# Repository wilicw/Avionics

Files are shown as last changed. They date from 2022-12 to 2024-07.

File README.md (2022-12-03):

# Avionics System

## Get Started

### [Install PlatformIO CLI](https://docs.platformio.org/en/latest/)

### Build Source Code

```
make
```

### Upload

```
make upload
```

## System Architecture

## [LICENSE](https://github.com/NCKU-ISP/Avionics/blob/main/LICENSE)

## Contact Us

To report any bugs or commit any new features, please create a new pull request and describe the issues in detail. If you are interested in our project and want to support us, please contact us with the following email: e94066157@gs.ncku.edu.tw, thanks!

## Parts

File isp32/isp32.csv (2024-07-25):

Source: | /Users/wilicw/Projects/Avionics-PCB/isp32/isp32.kicad_sch
Date: | Tuesday, June 04, 2024 at 09:10:36 PM
Tool: | Eeschema 7.0.11
Generator: | /Applications/KiCad/KiCad.app/Contents/SharedSupport/plugins/bom_csv_grouped_by_value.py
Component Count: | 85
Collated Components:
Item | Qty | Reference(s) | Value | LibPart | Footprint | Datasheet | DNP | MANUFACTURER | MAXIMUM_PACKAGE_HEIGHT | PARTREV | STANDARD | Sim.Device | Sim.Pins
1 | 6 | C3, C9, C11, C13, C16, C23 | 100n | Device:C_Small | Capacitor_SMD:C_0603_1608Metric | ~
2 | 1 | C5 | 100n | Device:C_Small | Capacitor_SMD:C_0805_2012Metric | ~
3 | 2 | C6, C10 | 22u | Device:C_Small | Capacitor_SMD:C_0603_1608Metric | ~
4 | 1 | C12 | 220u | Device:C_Small | Capacitor_Tantalum_SMD:CP_EIA-3528-12_Kemet-T | ~
5 | 2 | C14, C22 | 1u | Device:C_Small | Capacitor_SMD:C_0603_1608Metric | ~
6 | 1 | C15 | 10u | Device:C_Small | Capacitor_SMD:C_0805_2012Metric | ~
7 | 1 | D1 | Zener | Device:D_Zener_Small | Diode_SMD:D_SOD-123 | ~
8 | 1 | D2 | F0_LED | Device:LED_Small | LED_SMD:LED_0603_1608Metric | ~
9 | 1 | D3 | ESP_LED | Device:LED_Small | LED_SMD:LED_0603_1608Metric | ~
10 | 1 | D4 | F1_LED | Device:LED_Small | LED_SMD:LED_0603_1608Metric | ~
11 | 1 | D5 | POWER | Device:LED_Small | LED_SMD:LED_0603_1608Metric | ~
12 | 1 | D6 | TVS | Device:D_TVS_Filled | Diode_SMD:D_SMB | ~
13 | 1 | D7 | WS2812B | LED:WS2812B | LED_SMD:LED_WS2812B_PLCC4_5.0x5.0mm_P3.2mm | https://cdn-shop.adafruit.com/datasheets/WS2812B.pdf
14 | 1 | D8 | D_Shockley | Device:D_Shockley | Diode_SMD:D_SOD-123 | ~
15 | 1 | D9 | D_Small | Device:D_Small | Diode_SMD:D_SOD-123 | ~ |  |  |  |  |  | D | 1=K 2=A
16 | 4 | H1, H2, H3, H4 | MountingHole_Pad | Mechanical:MountingHole_Pad | MountingHole:MountingHole_3.2mm_M3_ISO7380_Pad | ~
17 | 1 | J1 | BAT1 | Connector_Generic:Conn_01x02 | Connector_JST:JST_XH_S2B-XH-A-1_1x02_P2.50mm_Horizontal | ~
18 | 1 | J2 | ExtBoard | Connector_Generic_MountingPin:Conn_01x05_MountingPin | Connector_Molex:Molex_PicoBlade_53261-0571_1x05-1MP_P1.25mm_Horizontal | ~
19 | 1 | J3 | USB_C_Receptacle_USB2.0 | Connector:USB_C_Receptacle_USB2.0 | Connector_USB:USB_C_Receptacle_Palconn_UTC16-G | https://www.usb.org/sites/default/files/documents/usb_type-c.zip
20 | 1 | J4 | ADC | Connector_Generic:Conn_01x05 | Connector_PinHeader_1.27mm:PinHeader_1x05_P1.27mm_Vertical | ~
21 | 1 | J5 | GPS_ANT | Connector:Conn_Coaxial | Connector_Coaxial:U.FL_Hirose_U.FL-R-SMT-1_Vertical | ~
22 | 1 | J6 | F0 | Connector:Screw_Terminal_01x02 | TerminalBlock_Phoenix:TerminalBlock_Phoenix_MPT-0,5-2-2.54_1x02_P2.54mm_Horizontal | ~
23 | 1 | J7 | F1 | Connector:Screw_Terminal_01x02 | TerminalBlock_Phoenix:TerminalBlock_Phoenix_MPT-0,5-2-2.54_1x02_P2.54mm_Horizontal | ~
24 | 1 | J9 | ANT | Connector_Generic:Conn_01x01 | Connector_PinHeader_2.00mm:PinHeader_1x01_P2.00mm_Vertical | ~
25 | 1 | J10 | LoRa_ANT | Connector:Conn_Coaxial | Connector_Coaxial:U.FL_Hirose_U.FL-R-SMT-1_Vertical | ~
26 | 1 | J11 | Power Modules | Connector_Generic:Conn_01x04 | Connector_PinSocket_2.54mm:PinSocket_1x04_P2.54mm_Vertical | ~
27 | 1 | J12 | Micro_SD_Card | Connector:Micro_SD_Card | Connector_Card:microSD_HC_Wuerth_693072010801 | http://katalog.we-online.de/em/datasheet/693072010801.pdf
28 | 1 | J13 | VIN_SELECT | Connector_Generic:Conn_01x03 | Connector_PinHeader_2.54mm:PinHeader_1x03_P2.54mm_Vertical | ~
29 | 1 | J14 | BUZZ | Connector_Generic_MountingPin:Conn_01x02_MountingPin | Connector_Molex:Molex_PicoBlade_53261-0271_1x02-1MP_P1.25mm_Horizontal | ~
30 | 1 | L2 | 22u | Device:L_Small | Inductor_SMD:L_0805_2012Metric | ~
31 | 1 | LS1 | 5020 | KSSG33J12-3:KSSG33J12-3 | Buzzer:XDCR_KSSG33J12-3 |  |  | Kingstate | 2.2 mm | 1.4 | Manufacturer recommendations
32 | 4 | M1, M2, M3, M4 | Motor_Servo | Motor:Motor_Servo | Connector_PinHeader_2.54mm:PinHeader_1x03_P2.54mm_Vertical | http://forums.parallax.com/uploads/attachments/46831/74481.png
33 | 2 | Q1, Q4 | BSS138 | Transistor_FET:BSS138 | Package_TO_SOT_SMD:SOT-23 | https://www.onsemi.com/pub/Collateral/BSS138-D.PDF
34 | 1 | Q2 | S8050 | Device:Q_NPN_BCE | Package_TO_SOT_SMD:SOT-23 | ~
35 | 3 | Q3, Q5, Q6 | IRLML6402 | Transistor_FET:IRLML6402 | Package_TO_SOT_SMD:SOT-23 | https://www.infineon.com/dgdl/irlml6402pbf.pdf?fileId=5546d462533600a401535668d5c2263c
36 | 6 | R1, R2, R14, R15, R22, R25 | 10k | Device:R_Small | Resistor_SMD:R_0603_1608Metric | ~
37 | 1 | R3 | 100 | Device:R_Small | Resistor_SMD:R_0603_1608Metric | ~
38 | 2 | R4, R6 | 4k7 | Device:R_Small | Resistor_SMD:R_0603_1608Metric | ~
39 | 2 | R5, R7 | 5k1 | Device:R_Small | Resistor_SMD:R_0603_1608Metric | ~
40 | 1 | R12 | 22 | Device:R_Small | Resistor_SMD:R_0603_1608Metric | ~
41 | 4 | R16, R20, R23, R24 | 100K | Device:R_Small | Resistor_SMD:R_0603_1608Metric | ~
42 | 2 | R18, R19 | 1k | Device:R_Small | Resistor_SMD:R_0603_1608Metric | ~
43 | 1 | R26 | 100k | Device:R_Small | Resistor_SMD:R_0603_1608Metric | ~
44 | 1 | SW1 | RST | Switch:SW_Push | Button_Switch_SMD:SW_SPST_FSMSM | ~
45 | 1 | TP1 | 3V3 | Connector:TestPoint | TestPoint:TestPoint_Pad_D1.0mm | ~
46 | 1 | TP2 | TP-3V3 | Connector:TestPoint | TestPoint:TestPoint_Pad_D1.0mm | ~
47 | 1 | TP3 | SWDIO | Connector:TestPoint | TestPoint:TestPoint_Pad_D1.0mm | ~
48 | 1 | TP4 | SWCLK | Connector:TestPoint | TestPoint:TestPoint_Pad_D1.0mm | ~
49 | 1 | TP5 | GND | Connector:TestPoint | TestPoint:TestPoint_Pad_D1.0mm | ~
50 | 1 | U1 | AZ1117-3.3 | Regulator_Linear:AZ1117-3.3 | Package_TO_SOT_SMD:SOT-223-3_TabPin2 | https://www.diodes.com/assets/Datasheets/AZ1117.pdf
51 | 1 | U2 | BA05C | Regulator_Linear:AP2204R-5.0 | Package_TO_SOT_SMD:TO-252-2 | https://www.diodes.com/assets/Datasheets/AP2204.pdf
52 | 1 | U3 | STM32G030F6 | STM32G030F6:STM32G030F6 | Package_SO:TSSOP-20_4.4x6.5mm_P0.65mm
53 | 1 | U4 | LSM6DSM | Sensor_Motion:LSM6DSM | Package_LGA:LGA-14_3x2.5mm_P0.5mm_LayoutBorder3x4y | https://www.st.com/resource/en/datasheet/lsm6dsm.pdf
54 | 1 | U6 | 24LC32 | Memory_EEPROM:24LC32 | Package_SO:SOIC-8_3.9x4.9mm_P1.27mm | http://ww1.microchip.com/downloads/en/DeviceDoc/21072G.pdf
55 | 1 | U7 | NEO-XM | RF_GPS:NEO-M8M | RF_GPS:ublox_NEO | https://www.u-blox.com/sites/default/files/NEO-M8-FW3_DataSheet_%28UBX-15031086%29.pdf
56 | 1 | U8 | ESP32-S3-WROOM-1U | ESP32-S3-WROOM-1U:ESP32-S3-WROOM-1U | ESP32-S3-WROOM-1U:XCVR_ESP32-S3-WROOM-1U |  |  | Espressif | 3.35mm | v0.6 | Manufacturer Recommendations
57 | 1 | U9 | RFM98W-315S2 | RF_Module:RFM98W-315S2 | RF_Module:HOPERF_RFM9XW_SMD | https://www.hoperf.com/data/upload/portal/20181127/5bfcdb5e17543.pdf
58 | 1 | U10 | BMP280 | Sensor_Pressure:BMP280 | Package_LGA:Bosch_LGA-8_2x2.5mm_P0.65mm_ClockwisePinNumbering | https://ae-bst.resource.bosch.com/media/_tech/media/datasheets/BST-BMP280-DS001.pdf

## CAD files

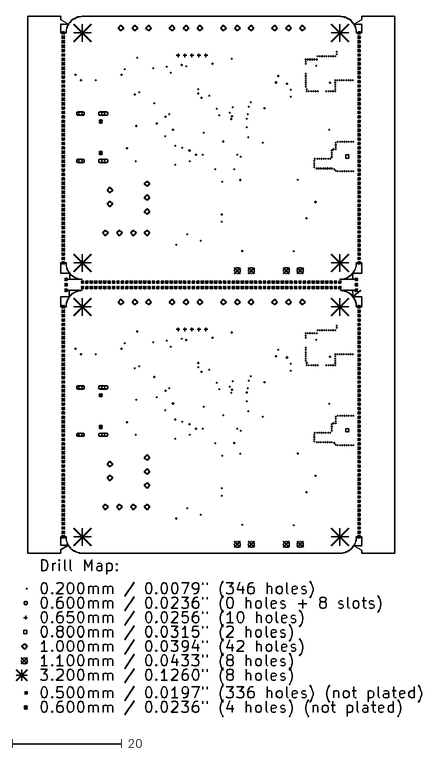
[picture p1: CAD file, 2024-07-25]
isp32/gerber/panel-drl_map.dxf
73.9 x 127.8

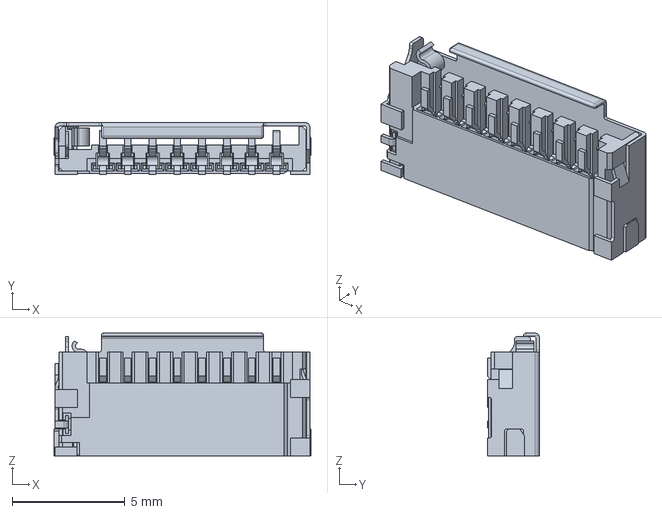
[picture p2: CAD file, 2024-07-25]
isp32/475710001.stp
11.4 x 2.30 x 5.45 mm

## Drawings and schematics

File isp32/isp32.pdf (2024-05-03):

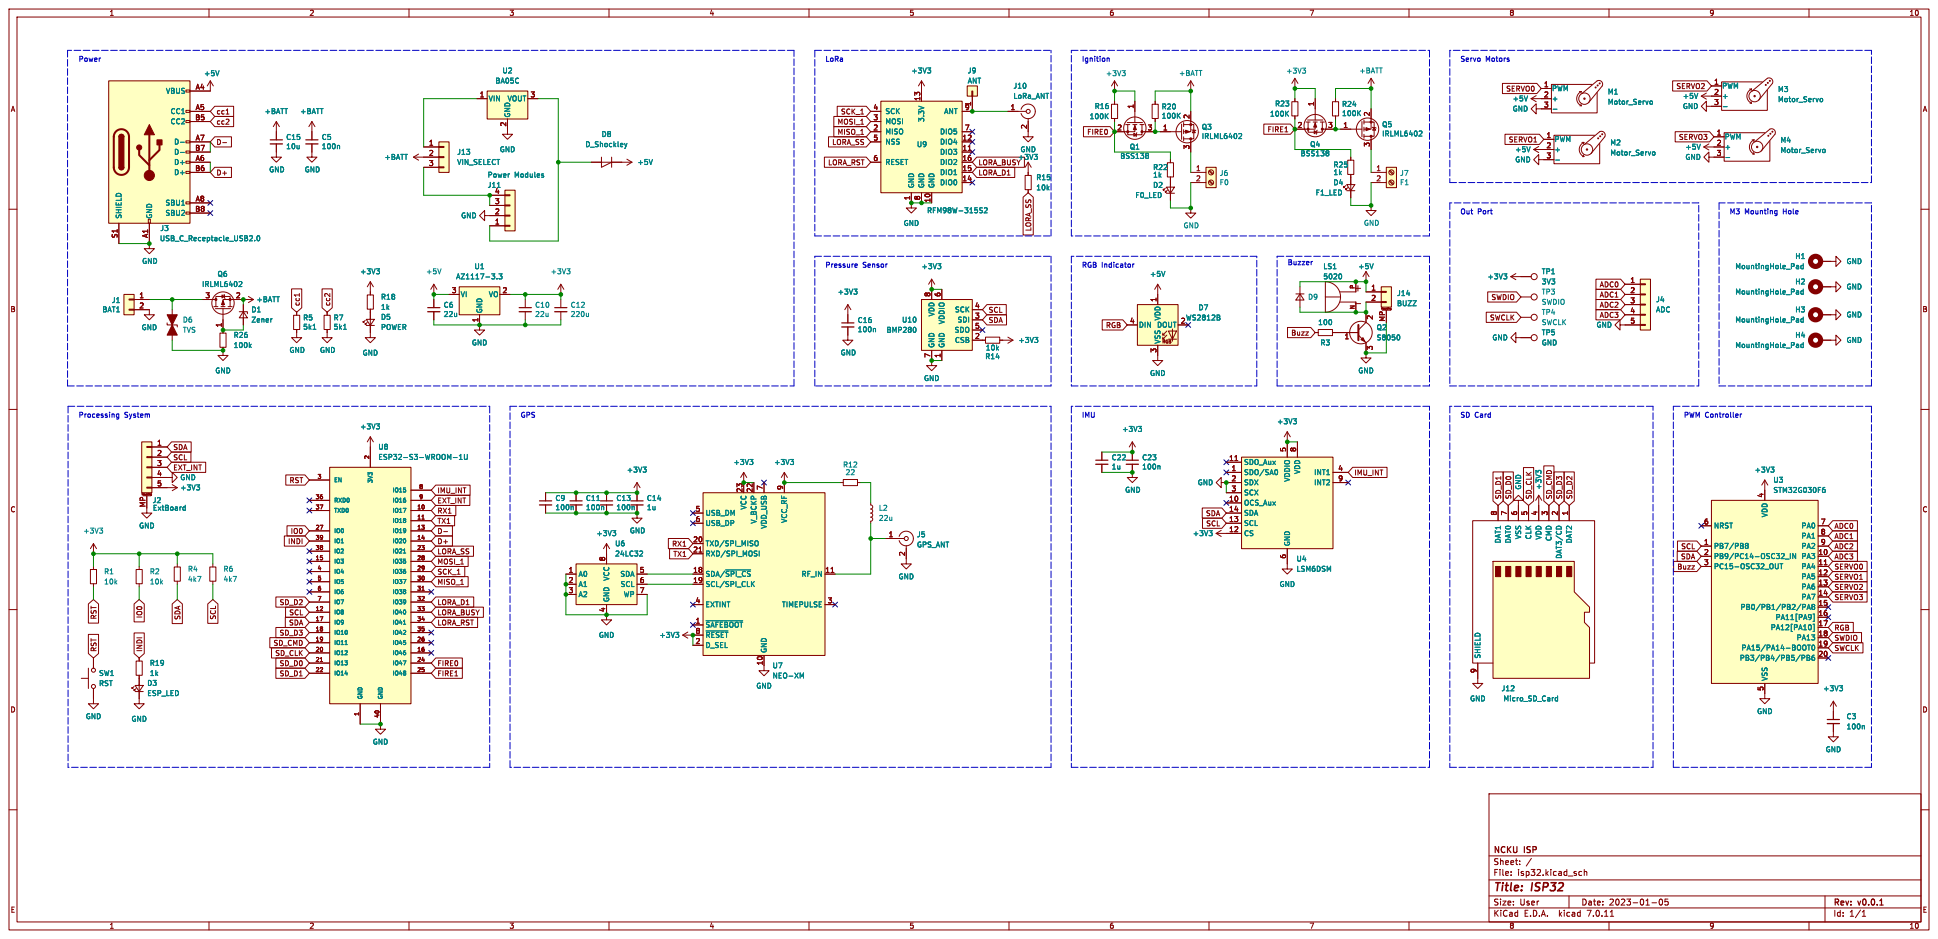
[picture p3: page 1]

2 VOUT 3 U2 BA05C GND GND GND GND GND

1 GND 10 DIO3 11 DIO4 12 3.3V 13 DIO0 14 DIO1 15 DIO2 16 MISO 2 MOSI 3 SCK 4 NSS 5 RESET 6 DIO5 7 GND

1 CSB 2 SDI 3 SCK 4 SDO 5 VDDIO

SDO/SA0 1 OCS_Aux 10 SDO_Aux 11 CS 12 SCL 13 SDA 14 SDX 2 SCX 3

4 SDA 5 SCL 6 WP 7 VCC

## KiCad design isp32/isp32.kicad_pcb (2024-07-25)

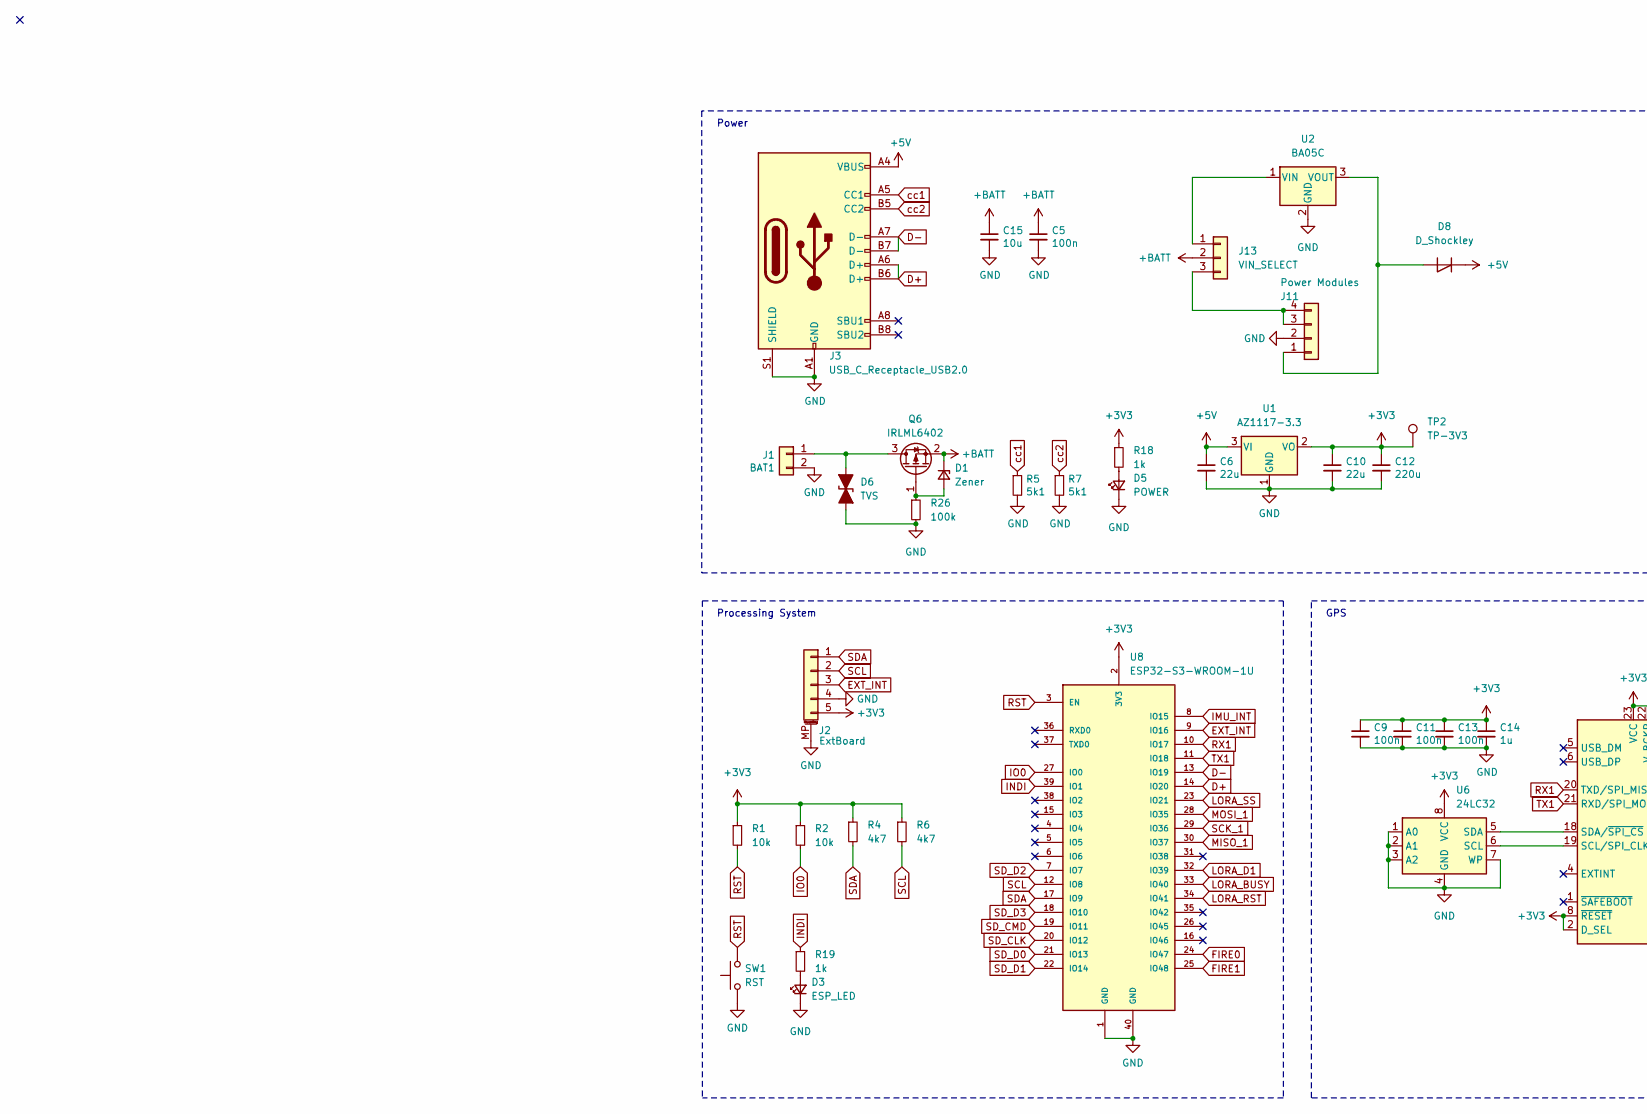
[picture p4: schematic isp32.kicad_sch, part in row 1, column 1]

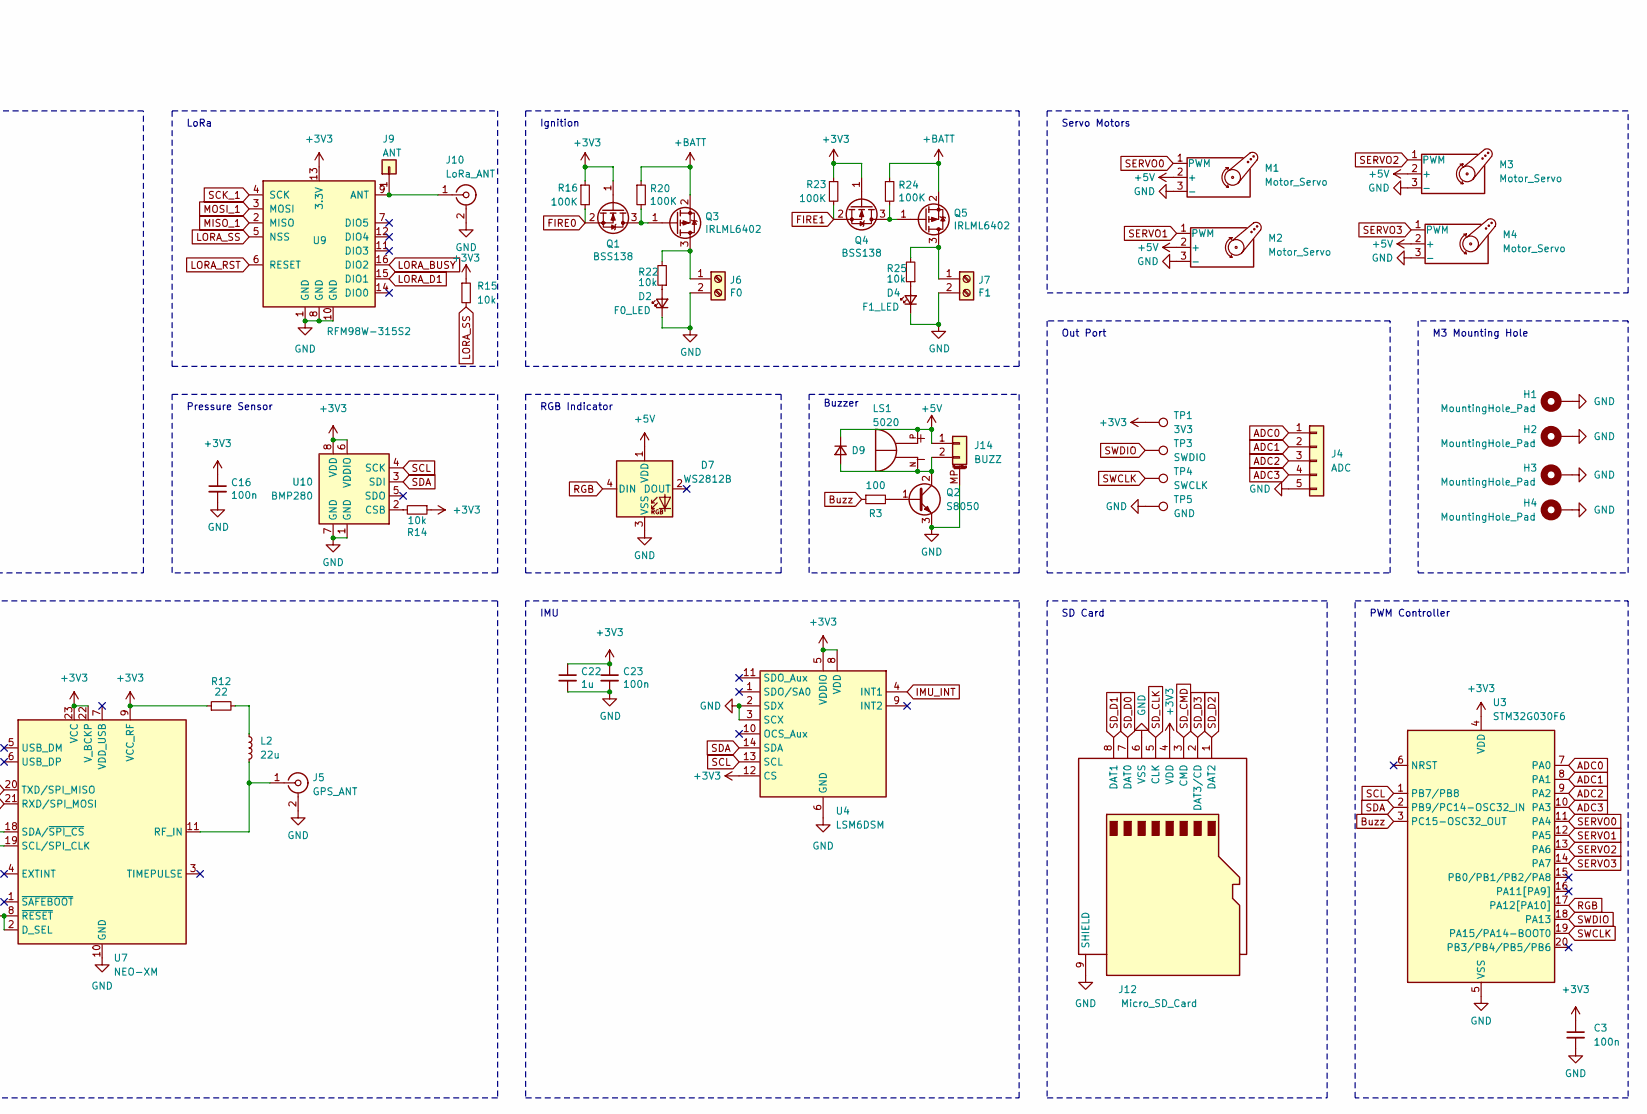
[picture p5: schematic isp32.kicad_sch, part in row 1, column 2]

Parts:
C3, C9, C11, C13, C16, C23: 100n; C_0603_1608Metric
C5: 100n; C_0805_2012Metric
C6, C10: 22u; C_0603_1608Metric
C12: 220u; CP_EIA-3528-12_Kemet-T
C14, C22: 1u; C_0603_1608Metric
C15: 10u; C_0805_2012Metric
D1: Zener; D_SOD-123
D2: F0_LED; LED_0603_1608Metric
D3: ESP_LED; LED_0603_1608Metric
D4: F1_LED; LED_0603_1608Metric
D5: POWER; LED_0603_1608Metric
D6: TVS; D_SMB
D7: WS2812B; LED_WS2812B_PLCC4_5.0x5.0mm_P3.2mm
D8: D_Shockley; D_SOD-123
D9: D_Small; D_SOD-123
H1, H2, H3, H4: MountingHole_Pad; MountingHole_3.2mm_M3_ISO7380_Pad
J1: BAT1; JST_XH_S2B-XH-A-1_1x02_P2.50mm_Horizontal
J2: ExtBoard; Molex_PicoBlade_53261-0571_1x05-1MP_P1.25mm_Horizontal
J3: USB_C_Receptacle_USB2.0; USB_C_Receptacle_Palconn_UTC16-G
J4: ADC; PinHeader_1x05_P1.27mm_Vertical
J5: GPS_ANT; U.FL_Hirose_U.FL-R-SMT-1_Vertical
J6: F0; TerminalBlock_Phoenix_MPT-0,5-2-2.54_1x02_P2.54mm_Horizontal
J7: F1; TerminalBlock_Phoenix_MPT-0,5-2-2.54_1x02_P2.54mm_Horizontal
J9: ANT; PinHeader_1x01_P2.00mm_Vertical
J10: LoRa_ANT; U.FL_Hirose_U.FL-R-SMT-1_Vertical
J11: Power Modules; PinSocket_1x04_P2.54mm_Vertical
J12: Micro_SD_Card; microSD_HC_Wuerth_693072010801
J13: VIN_SELECT; PinHeader_1x03_P2.54mm_Vertical
J14: BUZZ; Molex_PicoBlade_53261-0271_1x02-1MP_P1.25mm_Horizontal
L2: 22u; L_0805_2012Metric
LS1: 5020; XDCR_KSSG33J12-3; PARTREV 1.4
M1, M2, M3, M4: Motor_Servo; PinHeader_1x03_P2.54mm_Vertical
Q1, Q4: BSS138; SOT-23
Q2: S8050; SOT-23
Q3, Q5, Q6: IRLML6402; SOT-23
R1, R2, R14, R15, R22, R25: 10k; R_0603_1608Metric
R3: 100; R_0603_1608Metric
R4, R6: 4k7; R_0603_1608Metric
R5, R7: 5k1; R_0603_1608Metric
R12: 22; R_0603_1608Metric
R16, R20, R23, R24: 100K; R_0603_1608Metric
R18, R19: 1k; R_0603_1608Metric
R26: 100k; R_0603_1608Metric
SW1: RST; SW_SPST_FSMSM
TP1: 3V3; TestPoint_Pad_D1.0mm
TP2: TP-3V3; TestPoint_Pad_D1.0mm
TP3: SWDIO; TestPoint_Pad_D1.0mm
TP4: SWCLK; TestPoint_Pad_D1.0mm
TP5: GND; TestPoint_Pad_D1.0mm
U1: AZ1117-3.3; SOT-223-3_TabPin2
U2: BA05C; TO-252-2
U3: STM32G030F6; TSSOP-20_4.4x6.5mm_P0.65mm
U4: LSM6DSM; LGA-14_3x2.5mm_P0.5mm_LayoutBorder3x4y
U6: 24LC32; SOIC-8_3.9x4.9mm_P1.27mm
U7: NEO-XM; ublox_NEO
U8: ESP32-S3-WROOM-1U; XCVR_ESP32-S3-WROOM-1U; PARTREV v0.6
U9: RFM98W-315S2; HOPERF_RFM9XW_SMD
U10: BMP280; Bosch_LGA-8_2x2.5mm_P0.65mm_ClockwisePinNumbering

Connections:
+3V3: C3.1, C9.1, C10.1, C11.1, C12.1, C13.1, C14.1, C16.1, C22.1, C23.1, J2.5, J12.4 (VDD), Q1.1 (G), Q4.1 (G), R1.1, R2.1, R4.1, R6.1, R12.1, R14.1, R15.1, R16.1, R18.1, R23.1, TP1.1, TP2.1, U1.2 (VO), U3.4 (VDD), U4.5 (VDDIO), U4.8 (VDD), U4.12 (CS), U6.8 (VCC), U7.2 (D_SEL), U7.8 (~RESET), U7.9 (VCC_RF), U7.22 (V_BCKP), U7.23 (VCC), U8.2 (3V3), U9.13 (3.3V), U10.6 (VDDIO), U10.8 (VDD)
+5V: C6.1, D7.1 (VDD), D8.1 (K), D9.1 (K), J3.A4 (VBUS), J3.A9 (VBUS), J3.B4 (VBUS), J3.B9 (VBUS), J14.1, LS1.P, M1.2 (+), M2.2 (+), M3.2 (+), M4.2 (+), U1.3 (VI)
+BATT: C5.1, C15.1, D1.1 (K), J13.2, Q3.2 (S), Q5.2 (S), Q6.2 (S), R20.1, R24.1
ADC0: J4.1, U3.7 (PA0)
ADC1: J4.2, U3.8 (PA1)
ADC2: J4.3, U3.9 (PA2)
ADC3: J4.4, U3.10 (PA3)
Buzz: R3.1, U3.3 (PC15-OSC32_OUT)
D+: J3.A6 (D+), J3.B6 (D+), U8.14 (IO20)
D-: J3.A7 (D-), J3.B7 (D-), U8.13 (IO19)
EXT_INT: J2.3, U8.9 (IO16)
FIRE0: Q1.2 (S), R16.2, U8.24 (IO47)
FIRE1: Q4.2 (S), R23.2, U8.25 (IO48)
GND: C3.2, C5.2, C6.2, C9.2, C10.2, C11.2, C12.2, C13.2, C14.2, C15.2, C16.2, C22.2, C23.2, D2.1 (K), D3.1 (K), D4.1 (K), D5.1 (K), D6.1 (A1), D7.3 (VSS), H1.1, H2.1, H3.1, H4.1, J1.2, J2.4, J2.MP (MountPin), J3.A1 (GND), J3.A12 (GND), J3.B1 (GND), J3.B12 (GND), J3.S1 (SHIELD), J4.5, J5.2 (Ext), J6.2, J7.2, J10.2 (Ext), J11.2, J12.6 (VSS), J12.9 (SHIELD), J14.MP (MountPin), M1.3 (-), M2.3 (-), M3.3 (-), M4.3 (-), Q2.3 (E), R5.2, R7.2, R26.2, SW1.1, TP5.1, U1.1 (GND), U2.2 (GND), U3.5 (VSS), U4.2 (SDX), U4.3 (SCX), U4.6 (GND), U4.7 (GND), U6.1 (A0), U6.2 (A1), U6.3 (A2), U6.4 (GND), U6.7 (WP), U7.10 (GND), U7.12 (GND), U7.13 (GND), U7.24 (GND), U8.1 (GND), U8.40 (GND), U8.41_1 (GND), U8.41_2 (GND), U8.41_3 (GND), U8.41_4 (GND), U8.41_5 (GND), U8.41_6 (GND), U8.41_7 (GND), U8.41_8 (GND), U8.41_9 (GND), U9.1 (GND), U9.8 (GND), U9.10 (GND), U10.1 (GND), U10.7 (GND)
IMU_INT: U4.4 (INT1), U8.8 (IO15)
INDI: R19.1, U8.39 (IO1)
IO0: R2.2, U8.27 (IO0)
LORA_BUSY: U8.33 (IO40), U9.16 (DIO2)
LORA_D1: U8.32 (IO39), U9.15 (DIO1)
LORA_RST: U8.34 (IO41), U9.6 (RESET)
LORA_SS: R15.2, U8.23 (IO21), U9.5 (NSS)
MISO_1: U8.30 (IO37), U9.2 (MISO)
MOSI_1: U8.28 (IO35), U9.3 (MOSI)
unnamed: D1.2 (A), Q6.1 (G), R26.1
unnamed: D2.2 (A), R22.1
unnamed: D3.2 (A), R19.2
unnamed: D4.2 (A), R25.1
unnamed: D5.2 (A), R18.2
unnamed: D6.2 (A2), J1.1, Q6.3 (D)
unnamed: D8.2 (A), J11.1, U2.3 (VOUT)
unnamed: D9.2 (A), J14.2, LS1.N, Q2.2 (C)
unnamed: J5.1 (In), L2.2, U7.11 (RF_IN)
unnamed: J6.1, Q3.3 (D), R22.2
unnamed: J7.1, Q5.3 (D), R25.2
unnamed: J9.1, J10.1 (In), U9.9 (ANT)
unnamed: J11.3, J11.4, J13.3
unnamed: J13.1, U2.1 (VIN)
unnamed: L2.1, R12.2
unnamed: Q1.3 (D), Q3.1 (G), R20.2
unnamed: Q2.1 (B), R3.2
unnamed: Q4.3 (D), Q5.1 (G), R24.2
unnamed: U6.6 (SCL), U7.19 (SCL/SPI_CLK)
unnamed: U6.5 (SDA), U7.18 (SDA/~SPI_CS)
unnamed: R14.2, U10.2 (CSB)
RGB: D7.4 (DIN), U3.17 (PA12[PA10])
RST: R1.2, SW1.2, U8.3 (EN)
RX1: U7.20 (TXD/SPI_MISO), U8.10 (IO17)
SCK_1: U8.29 (IO36), U9.4 (SCK)
SCL: J2.2, R6.2, U3.1 (PB7/PB8), U4.13 (SCL), U8.12 (IO8), U10.4 (SCK)
SDA: J2.1, R4.2, U3.2 (PB9/PC14-OSC32_IN), U4.14 (SDA), U8.17 (IO9), U10.3 (SDI)
SD_CLK: J12.5 (CLK), U8.20 (IO12)
SD_CMD: J12.3 (CMD), U8.19 (IO11)
SD_D0: J12.7 (DAT0), U8.21 (IO13)
SD_D1: J12.8 (DAT1), U8.22 (IO14)
SD_D2: J12.1 (DAT2), U8.7 (IO7)
SD_D3: J12.2 (DAT3/CD), U8.18 (IO10)
SERVO0: M1.1 (PWM), U3.11 (PA4)
SERVO1: M2.1 (PWM), U3.12 (PA5)
SERVO2: M3.1 (PWM), U3.13 (PA6)
SERVO3: M4.1 (PWM), U3.14 (PA7)
SWCLK: TP4.1, U3.19 (PA15/PA14-BOOT0)
SWDIO: TP3.1, U3.18 (PA13)
TX1: U7.21 (RXD/SPI_MOSI), U8.11 (IO18)
cc1: J3.A5 (CC1), R5.1
cc2: J3.B5 (CC2), R7.1

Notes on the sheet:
IMU
PWM Controller
Ignition
M3 Mounting Hole
Servo Motors
RGB Indicator
Out Port
Buzzer
Processing System
Pressure Sensor
LoRa
GPS
SD Card
Power

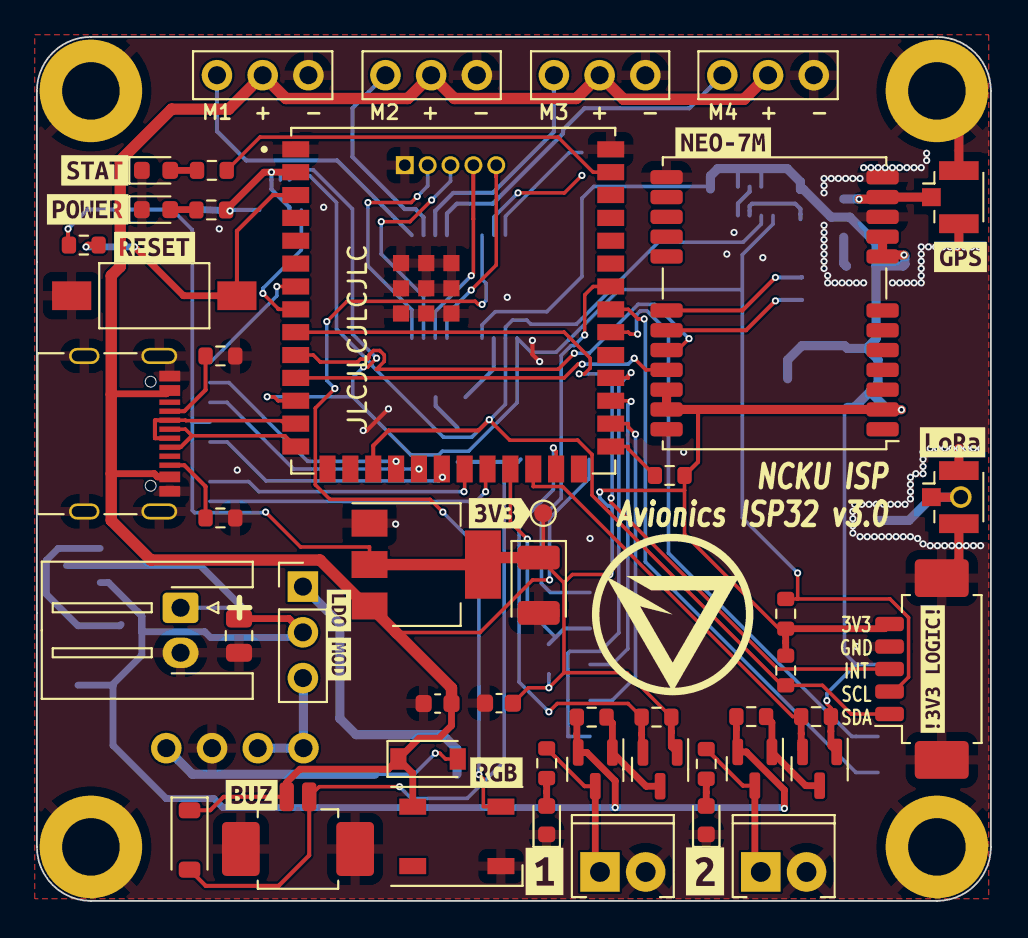
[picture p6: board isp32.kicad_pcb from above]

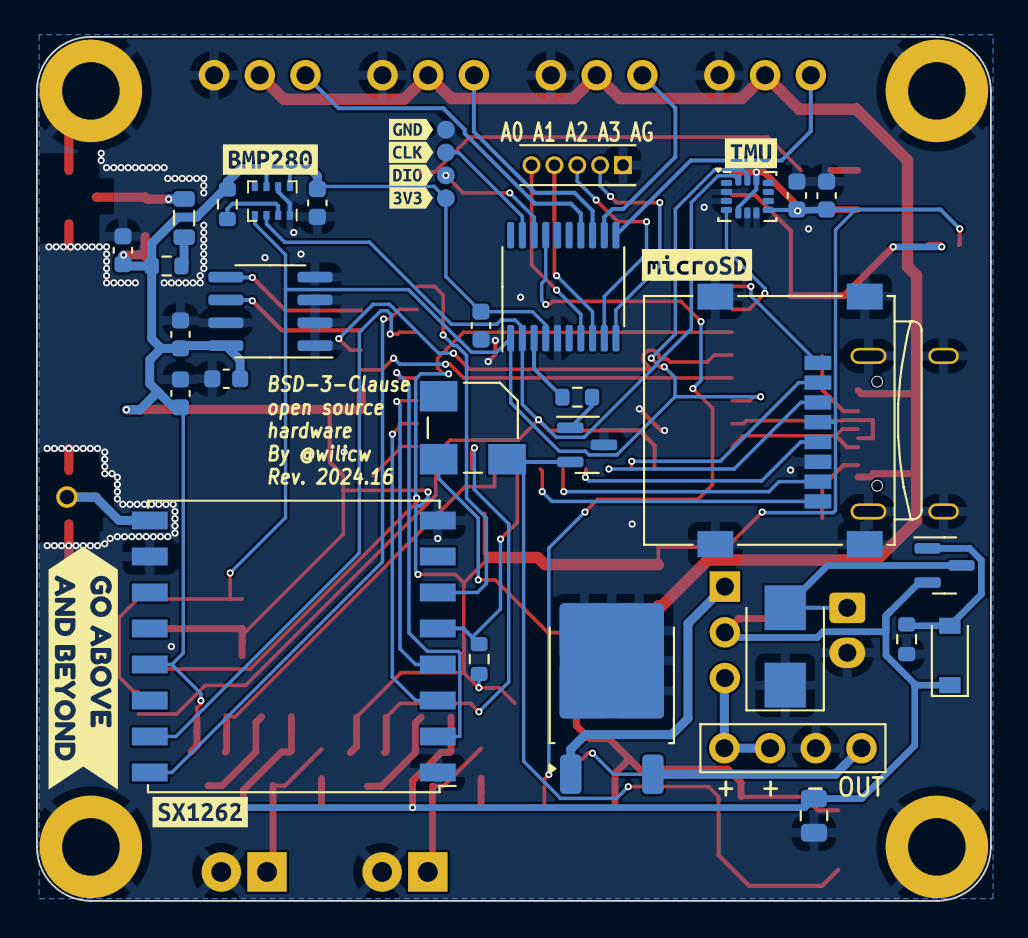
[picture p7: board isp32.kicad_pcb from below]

Board: 2 copper layers, 53.0 x 48.0 mm, 108 parts (43 on the bottom side), 65 nets.

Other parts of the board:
kibuzzard-63CD1E7F: G***; kibuzzard-63CD1E7F
kibuzzard-63CD1E61: G***; kibuzzard-63CD1E61
kibuzzard-63CD1EC0: G***; kibuzzard-63CD1EC0
kibuzzard-63CD1EC5: G***; kibuzzard-63CD1EC5
kibuzzard-63CD04EB: G***; kibuzzard-63CD04EB
kibuzzard-63CD04FB: G***; kibuzzard-63CD04FB
kibuzzard-641A73AC: G***; kibuzzard-641A73AC
kibuzzard-641A73E5: G***; kibuzzard-641A73E5
kibuzzard-641A73FA: G***; kibuzzard-641A73FA
kibuzzard-641A737F: G***; kibuzzard-641A737F
kibuzzard-641A7395: G***; kibuzzard-641A7395
kibuzzard-641A7704: G***; kibuzzard-641A7704
kibuzzard-642D97EE: G***; kibuzzard-642D97EE
kibuzzard-661FABB5: G***; kibuzzard-661FABB5
kibuzzard-661FAECF: G***; kibuzzard-661FAECF
kibuzzard-661FBC0A: G***; kibuzzard-661FBC0A
kibuzzard-661FBC21: G***; kibuzzard-661FBC21
kibuzzard-66439A83: G***; kibuzzard-66439A83
kibuzzard-66439ACD: G***; kibuzzard-66439ACD
kibuzzard-66439AF0: G***; kibuzzard-66439AF0
kibuzzard-66439B8F: G***; kibuzzard-66439B8F
kibuzzard-66439B33: G***; kibuzzard-66439B33
kibuzzard-66439C31: G***; kibuzzard-66439C31

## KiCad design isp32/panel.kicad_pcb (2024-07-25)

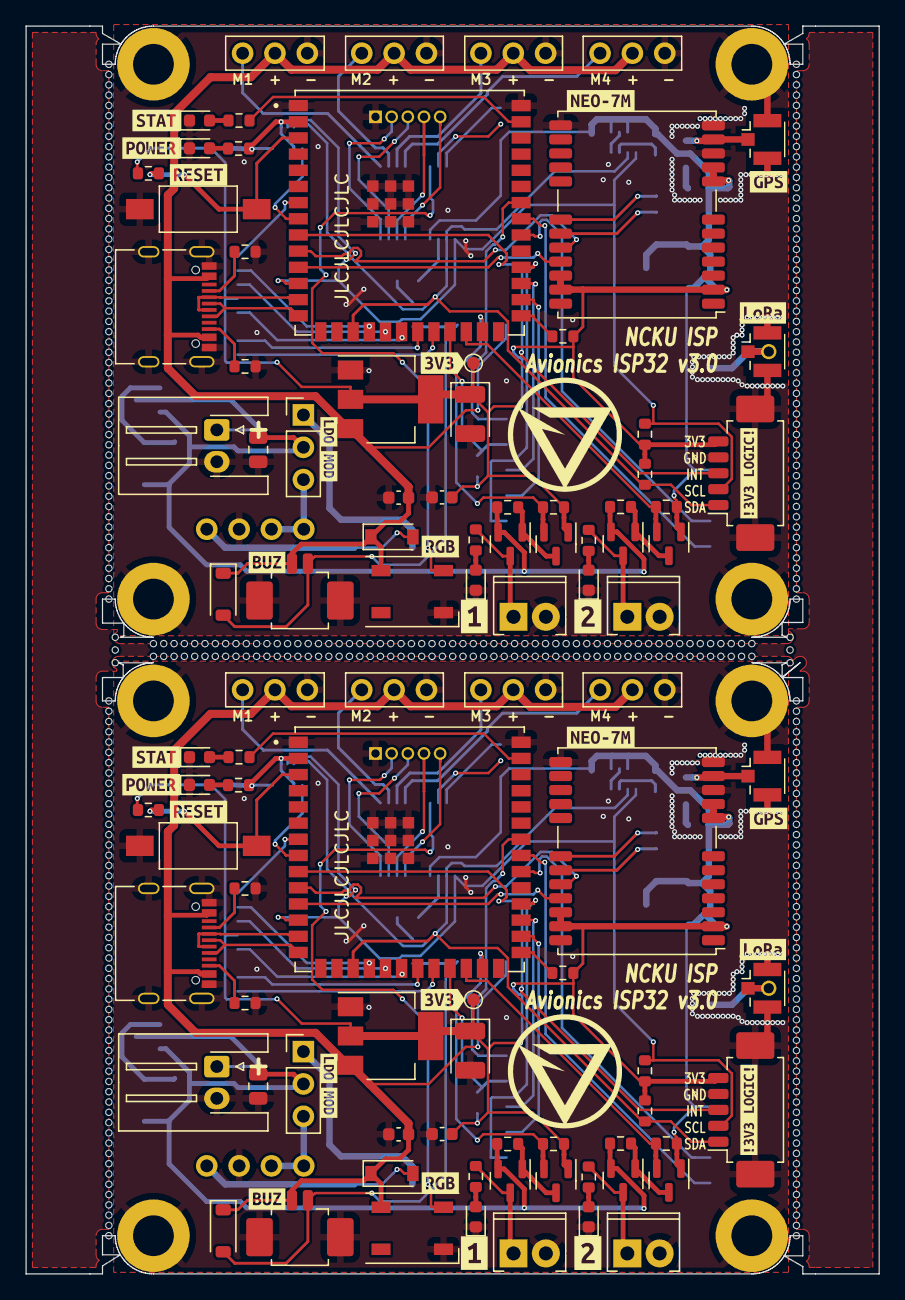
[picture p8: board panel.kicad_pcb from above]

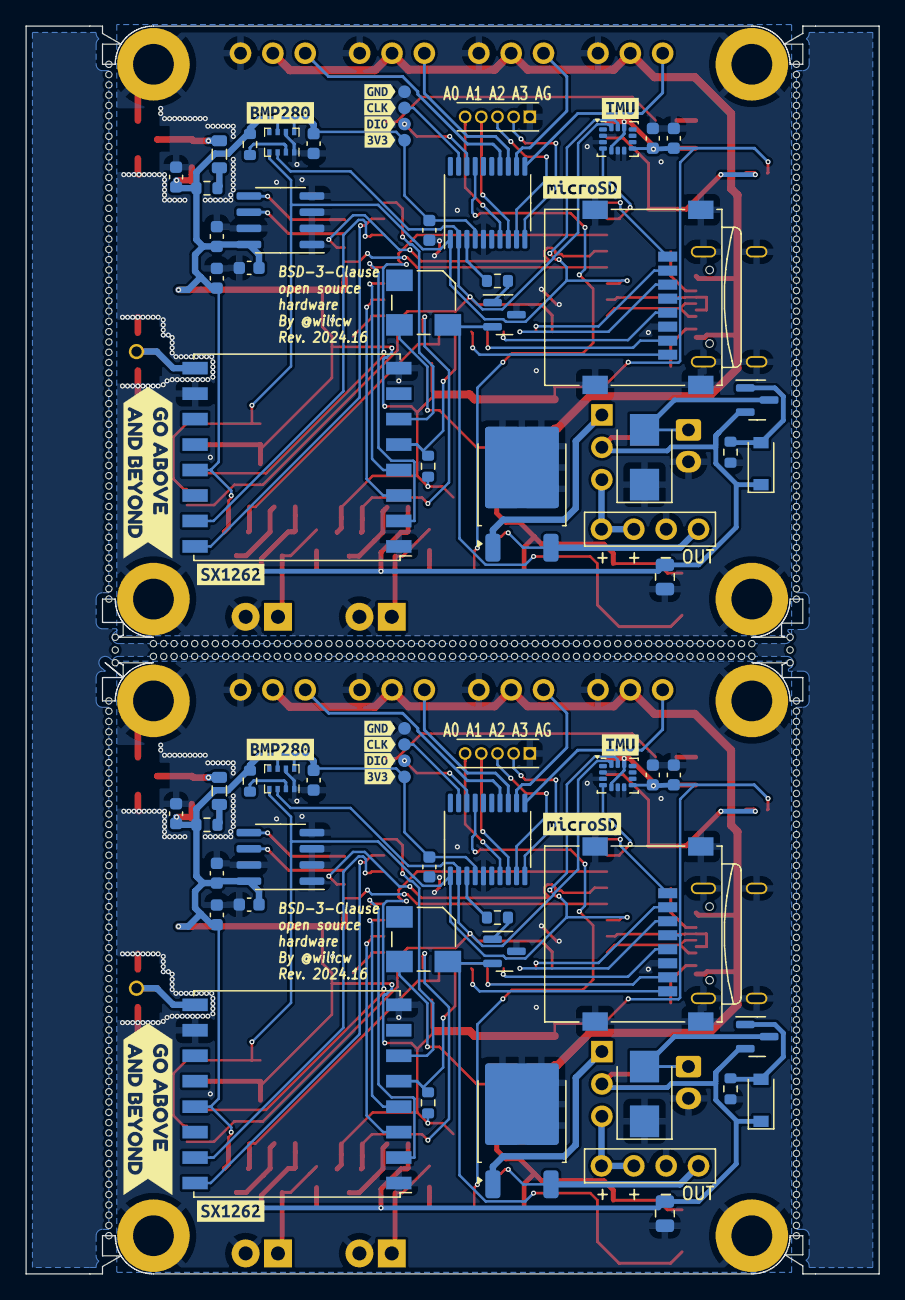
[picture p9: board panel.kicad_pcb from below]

Board: 2 copper layers, 67.0 x 98.0 mm, 552 parts (86 on the bottom side), 130 nets.

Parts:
C3, C3#2, C9, C9#2, C11, C11#2, C13, C13#2, C16, C16#2, C23, C23#2: 100n; C_0603_1608Metric
C5, C5#2: 100n; C_0805_2012Metric
C6, C6#2, C10, C10#2: 22u; C_0603_1608Metric
C12, C12#2: 220u; CP_EIA-3528-12_Kemet-T
C14, C14#2, C22, C22#2: 1u; C_0603_1608Metric
C15, C15#2: 10u; C_0805_2012Metric
D1, D1#2: Zener; D_SOD-123
D2, D2#2: F0_LED; LED_0603_1608Metric
D3, D3#2: ESP_LED; LED_0603_1608Metric
D4, D4#2: F1_LED; LED_0603_1608Metric
D5, D5#2: POWER; LED_0603_1608Metric
D6, D6#2: TVS; D_SMB
D7, D7#2: WS2812B; LED_WS2812B_PLCC4_5.0x5.0mm_P3.2mm
D8, D8#2: D_Shockley; D_SOD-123
D9, D9#2: D_Small; D_SOD-123
H1, H1#2, H2, H2#2, H3, H3#2, H4, H4#2: MountingHole_Pad; MountingHole_3.2mm_M3_ISO7380_Pad
J1, J1#2: BAT1; JST_XH_S2B-XH-A-1_1x02_P2.50mm_Horizontal
J2, J2#2: ExtBoard; Molex_PicoBlade_53261-0571_1x05-1MP_P1.25mm_Horizontal
J3, J3#2: USB_C_Receptacle_USB2.0; USB_C_Receptacle_Palconn_UTC16-G
J4, J4#2: ADC; PinHeader_1x05_P1.27mm_Vertical
J5, J5#2: GPS_ANT; U.FL_Hirose_U.FL-R-SMT-1_Vertical
J6, J6#2: F0; TerminalBlock_Phoenix_MPT-0,5-2-2.54_1x02_P2.54mm_Horizontal
J7, J7#2: F1; TerminalBlock_Phoenix_MPT-0,5-2-2.54_1x02_P2.54mm_Horizontal
J9, J9#2: ANT; PinHeader_1x01_P2.00mm_Vertical
J10, J10#2: LoRa_ANT; U.FL_Hirose_U.FL-R-SMT-1_Vertical
J11, J11#2: Power Modules; PinSocket_1x04_P2.54mm_Vertical
J12, J12#2: Micro_SD_Card; microSD_HC_Wuerth_693072010801
J13, J13#2: VIN_SELECT; PinHeader_1x03_P2.54mm_Vertical
J14, J14#2: BUZZ; Molex_PicoBlade_53261-0271_1x02-1MP_P1.25mm_Horizontal
KiKit_MB_1_1, KiKit_MB_1_2, KiKit_MB_1_3, KiKit_MB_1_4, KiKit_MB_1_5, KiKit_MB_1_6, KiKit_MB_1_7, KiKit_MB_1_8, KiKit_MB_1_9, KiKit_MB_1_10, KiKit_MB_1_11, KiKit_MB_1_12, KiKit_MB_1_13, KiKit_MB_1_14, KiKit_MB_1_15, KiKit_MB_1_16, KiKit_MB_1_17, KiKit_MB_1_18, KiKit_MB_1_19, KiKit_MB_1_20, KiKit_MB_1_21, KiKit_MB_1_22, KiKit_MB_1_23, KiKit_MB_1_24, KiKit_MB_1_25, KiKit_MB_1_26, KiKit_MB_1_27, KiKit_MB_1_28, KiKit_MB_1_29, KiKit_MB_1_30, KiKit_MB_1_31, KiKit_MB_1_32, KiKit_MB_1_33, KiKit_MB_1_34, KiKit_MB_1_35, KiKit_MB_1_36, KiKit_MB_1_37, KiKit_MB_1_38, KiKit_MB_1_39, KiKit_MB_1_40, KiKit_MB_1_41, KiKit_MB_1_42, KiKit_MB_1_43, KiKit_MB_1_44, KiKit_MB_1_45, KiKit_MB_1_46, KiKit_MB_1_47, KiKit_MB_1_48, KiKit_MB_1_49, KiKit_MB_1_50, KiKit_MB_1_51, KiKit_MB_1_52, KiKit_MB_1_53, KiKit_MB_2_1, KiKit_MB_2_2, KiKit_MB_2_3, KiKit_MB_2_4, KiKit_MB_2_5, KiKit_MB_2_6, KiKit_MB_2_7, KiKit_MB_2_8, KiKit_MB_2_9, KiKit_MB_2_10, KiKit_MB_2_11, KiKit_MB_2_12, KiKit_MB_2_13, KiKit_MB_2_14, KiKit_MB_2_15, KiKit_MB_2_16, KiKit_MB_2_17, KiKit_MB_2_18, KiKit_MB_2_19, KiKit_MB_2_20, KiKit_MB_2_21, KiKit_MB_2_22, KiKit_MB_2_23, KiKit_MB_2_24, KiKit_MB_2_25, KiKit_MB_2_26, KiKit_MB_2_27, KiKit_MB_2_28, KiKit_MB_2_29, KiKit_MB_2_30, KiKit_MB_2_31, KiKit_MB_2_32, KiKit_MB_2_33, KiKit_MB_2_34, KiKit_MB_2_35, KiKit_MB_2_36, KiKit_MB_2_37, KiKit_MB_2_38, KiKit_MB_2_39, KiKit_MB_2_40, KiKit_MB_2_41, KiKit_MB_2_42, KiKit_MB_2_43, KiKit_MB_2_44, KiKit_MB_2_45, KiKit_MB_2_46, KiKit_MB_2_47, KiKit_MB_2_48, KiKit_MB_2_49, KiKit_MB_2_50, KiKit_MB_2_51, KiKit_MB_2_52, KiKit_MB_2_53, KiKit_MB_2_54, KiKit_MB_2_55, KiKit_MB_2_56, KiKit_MB_2_57, KiKit_MB_2_58, KiKit_MB_2_59, KiKit_MB_3_1, KiKit_MB_3_2, KiKit_MB_3_3, KiKit_MB_3_4, KiKit_MB_3_5, KiKit_MB_3_6, KiKit_MB_3_7, KiKit_MB_3_8, KiKit_MB_3_9, KiKit_MB_3_10, KiKit_MB_3_11, KiKit_MB_3_12, KiKit_MB_3_13, KiKit_MB_3_14, KiKit_MB_3_15, KiKit_MB_3_16, KiKit_MB_3_17, KiKit_MB_3_18, KiKit_MB_3_19, KiKit_MB_3_20, KiKit_MB_3_21, KiKit_MB_3_22, KiKit_MB_3_23, KiKit_MB_3_24, KiKit_MB_3_25, KiKit_MB_3_26, KiKit_MB_3_27, KiKit_MB_3_28, KiKit_MB_3_29, KiKit_MB_3_30, KiKit_MB_3_31, KiKit_MB_3_32, KiKit_MB_3_33, KiKit_MB_3_34, KiKit_MB_3_35, KiKit_MB_3_36, KiKit_MB_3_37, KiKit_MB_3_38, KiKit_MB_3_39, KiKit_MB_3_40, KiKit_MB_3_41, KiKit_MB_3_42, KiKit_MB_3_43, KiKit_MB_3_44, KiKit_MB_3_45, KiKit_MB_3_46, KiKit_MB_3_47, KiKit_MB_3_48, KiKit_MB_3_49, KiKit_MB_3_50, KiKit_MB_3_51, KiKit_MB_3_52, KiKit_MB_3_53, KiKit_MB_4_1, KiKit_MB_4_2, KiKit_MB_4_3, KiKit_MB_4_4, KiKit_MB_4_5, KiKit_MB_4_6, KiKit_MB_4_7, KiKit_MB_4_8, KiKit_MB_4_9, KiKit_MB_4_10, KiKit_MB_4_11, KiKit_MB_4_12, KiKit_MB_4_13, KiKit_MB_4_14, KiKit_MB_4_15, KiKit_MB_4_16, KiKit_MB_4_17, KiKit_MB_4_18, KiKit_MB_4_19, KiKit_MB_4_20, KiKit_MB_4_21, KiKit_MB_4_22, KiKit_MB_4_23, KiKit_MB_4_24, KiKit_MB_4_25, KiKit_MB_4_26, KiKit_MB_4_27, KiKit_MB_4_28, KiKit_MB_4_29, KiKit_MB_4_30, KiKit_MB_4_31, KiKit_MB_4_32, KiKit_MB_4_33, KiKit_MB_4_34, KiKit_MB_4_35, KiKit_MB_4_36, KiKit_MB_4_37, KiKit_MB_4_38, KiKit_MB_4_39, KiKit_MB_4_40, KiKit_MB_4_41, KiKit_MB_4_42, KiKit_MB_4_43, KiKit_MB_4_44, KiKit_MB_4_45, KiKit_MB_4_46, KiKit_MB_4_47, KiKit_MB_4_48, KiKit_MB_4_49, KiKit_MB_4_50, KiKit_MB_4_51, KiKit_MB_4_52, KiKit_MB_4_53, KiKit_MB_5_1, KiKit_MB_5_2, KiKit_MB_5_3, KiKit_MB_5_4, KiKit_MB_5_5, KiKit_MB_5_6, KiKit_MB_5_7, KiKit_MB_5_8, KiKit_MB_5_9, KiKit_MB_5_10, KiKit_MB_5_11, KiKit_MB_5_12, KiKit_MB_5_13, KiKit_MB_5_14, KiKit_MB_5_15, KiKit_MB_5_16, KiKit_MB_5_17, KiKit_MB_5_18, KiKit_MB_5_19, KiKit_MB_5_20, KiKit_MB_5_21, KiKit_MB_5_22, KiKit_MB_5_23, KiKit_MB_5_24, KiKit_MB_5_25, KiKit_MB_5_26, KiKit_MB_5_27, KiKit_MB_5_28, KiKit_MB_5_29, KiKit_MB_5_30, KiKit_MB_5_31, KiKit_MB_5_32, KiKit_MB_5_33, KiKit_MB_5_34, KiKit_MB_5_35, KiKit_MB_5_36, KiKit_MB_5_37, KiKit_MB_5_38, KiKit_MB_5_39, KiKit_MB_5_40, KiKit_MB_5_41, KiKit_MB_5_42, KiKit_MB_5_43, KiKit_MB_5_44, KiKit_MB_5_45, KiKit_MB_5_46, KiKit_MB_5_47, KiKit_MB_5_48, KiKit_MB_5_49, KiKit_MB_5_50, KiKit_MB_5_51, KiKit_MB_5_52, KiKit_MB_5_53, KiKit_MB_5_54, KiKit_MB_5_55, KiKit_MB_5_56, KiKit_MB_5_57, KiKit_MB_5_58, KiKit_MB_5_59, KiKit_MB_6_1, KiKit_MB_6_2, KiKit_MB_6_3, KiKit_MB_6_4, KiKit_MB_6_5, KiKit_MB_6_6, KiKit_MB_6_7, KiKit_MB_6_8, KiKit_MB_6_9, KiKit_MB_6_10, KiKit_MB_6_11, KiKit_MB_6_12, KiKit_MB_6_13, KiKit_MB_6_14, KiKit_MB_6_15, KiKit_MB_6_16, KiKit_MB_6_17, KiKit_MB_6_18, KiKit_MB_6_19, KiKit_MB_6_20, KiKit_MB_6_21, KiKit_MB_6_22, KiKit_MB_6_23, KiKit_MB_6_24, KiKit_MB_6_25, KiKit_MB_6_26, KiKit_MB_6_27, KiKit_MB_6_28, KiKit_MB_6_29, KiKit_MB_6_30, KiKit_MB_6_31, KiKit_MB_6_32, KiKit_MB_6_33, KiKit_MB_6_34, KiKit_MB_6_35, KiKit_MB_6_36, KiKit_MB_6_37, KiKit_MB_6_38, KiKit_MB_6_39, KiKit_MB_6_40, KiKit_MB_6_41, KiKit_MB_6_42, KiKit_MB_6_43, KiKit_MB_6_44, KiKit_MB_6_45, KiKit_MB_6_46, KiKit_MB_6_47, KiKit_MB_6_48, KiKit_MB_6_49, KiKit_MB_6_50, KiKit_MB_6_51, KiKit_MB_6_52, KiKit_MB_6_53, KiKit_MB_7_1, KiKit_MB_7_2, KiKit_MB_7_3, KiKit_MB_8_1, KiKit_MB_8_2, KiKit_MB_8_3: NPTH
L2, L2#2: 22u; L_0805_2012Metric
LS1, LS1#2: 5020; XDCR_KSSG33J12-3
M1, M1#2, M2, M2#2, M3, M3#2, M4, M4#2: Motor_Servo; PinHeader_1x03_P2.54mm_Vertical
Q1, Q1#2, Q4, Q4#2: BSS138; SOT-23
Q2, Q2#2: S8050; SOT-23
Q3, Q3#2, Q5, Q5#2, Q6, Q6#2: IRLML6402; SOT-23
R1, R1#2, R2, R2#2, R14, R14#2, R15, R15#2, R22, R22#2, R25, R25#2: 10k; R_0603_1608Metric
R3, R3#2: 100; R_0603_1608Metric
R4, R4#2, R6, R6#2: 4k7; R_0603_1608Metric
R5, R5#2, R7, R7#2: 5k1; R_0603_1608Metric
R12, R12#2: 22; R_0603_1608Metric
R16, R16#2, R20, R20#2, R23, R23#2, R24, R24#2: 100K; R_0603_1608Metric
R18, R18#2, R19, R19#2: 1k; R_0603_1608Metric
R26, R26#2: 100k; R_0603_1608Metric
SW1, SW1#2: RST; SW_SPST_FSMSM
TP1, TP1#2: 3V3; TestPoint_Pad_D1.0mm
TP2, TP2#2: TP-3V3; TestPoint_Pad_D1.0mm
TP3, TP3#2: SWDIO; TestPoint_Pad_D1.0mm
TP4, TP4#2: SWCLK; TestPoint_Pad_D1.0mm
TP5, TP5#2: GND; TestPoint_Pad_D1.0mm
U1, U1#2: AZ1117-3.3; SOT-223-3_TabPin2
U2, U2#2: BA05C; TO-252-2
U3, U3#2: STM32G030F6; TSSOP-20_4.4x6.5mm_P0.65mm
U4, U4#2: LSM6DSM; LGA-14_3x2.5mm_P0.5mm_LayoutBorder3x4y
U6, U6#2: 24LC32; SOIC-8_3.9x4.9mm_P1.27mm
U7, U7#2: NEO-XM; ublox_NEO
U8, U8#2: ESP32-S3-WROOM-1U; XCVR_ESP32-S3-WROOM-1U
U9, U9#2: RFM98W-315S2; HOPERF_RFM9XW_SMD
U10, U10#2: BMP280; Bosch_LGA-8_2x2.5mm_P0.65mm_ClockwisePinNumbering
kibuzzard-63CD1E7F, kibuzzard-63CD1E7F#2: G***; kibuzzard-63CD1E7F
kibuzzard-63CD1E61, kibuzzard-63CD1E61#2: G***; kibuzzard-63CD1E61
kibuzzard-63CD1EC0, kibuzzard-63CD1EC0#2: G***; kibuzzard-63CD1EC0
kibuzzard-63CD1EC5, kibuzzard-63CD1EC5#2: G***; kibuzzard-63CD1EC5
kibuzzard-63CD04EB, kibuzzard-63CD04EB#2: G***; kibuzzard-63CD04EB
kibuzzard-63CD04FB, kibuzzard-63CD04FB#2: G***; kibuzzard-63CD04FB
kibuzzard-641A73AC, kibuzzard-641A73AC#2: G***; kibuzzard-641A73AC
kibuzzard-641A73E5, kibuzzard-641A73E5#2: G***; kibuzzard-641A73E5
kibuzzard-641A73FA, kibuzzard-641A73FA#2: G***; kibuzzard-641A73FA
kibuzzard-641A737F, kibuzzard-641A737F#2: G***; kibuzzard-641A737F
kibuzzard-641A7395, kibuzzard-641A7395#2: G***; kibuzzard-641A7395
kibuzzard-641A7704, kibuzzard-641A7704#2: G***; kibuzzard-641A7704
kibuzzard-642D97EE, kibuzzard-642D97EE#2: G***; kibuzzard-642D97EE
kibuzzard-661FABB5, kibuzzard-661FABB5#2: G***; kibuzzard-661FABB5
kibuzzard-661FAECF, kibuzzard-661FAECF#2: G***; kibuzzard-661FAECF
kibuzzard-661FBC0A, kibuzzard-661FBC0A#2: G***; kibuzzard-661FBC0A
kibuzzard-661FBC21, kibuzzard-661FBC21#2: G***; kibuzzard-661FBC21
kibuzzard-66439A83, kibuzzard-66439A83#2: G***; kibuzzard-66439A83
kibuzzard-66439ACD, kibuzzard-66439ACD#2: G***; kibuzzard-66439ACD
kibuzzard-66439AF0, kibuzzard-66439AF0#2: G***; kibuzzard-66439AF0
kibuzzard-66439B8F, kibuzzard-66439B8F#2: G***; kibuzzard-66439B8F
kibuzzard-66439B33, kibuzzard-66439B33#2: G***; kibuzzard-66439B33
kibuzzard-66439C31, kibuzzard-66439C31#2: G***; kibuzzard-66439C31

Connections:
Board_0-+3V3: C3#2.1, C9.1, C10#2.1, C11.1, C12#2.1, C13#2.1, C14.1, C16.1, C22#2.1, C23.1, J2#2.5, J12#2.4 (VDD), Q1#2.1 (G), Q4#2.1 (G), R1.1, R2#2.1, R4#2.1, R6.1, R12.1, R14#2.1, R15.1, R16#2.1, R18#2.1, R23#2.1, TP1#2.1, TP2#2.1, U1#2.2 (VO), U3#2.4 (VDD), U4#2.5 (VDDIO), U4#2.8 (VDD), U4#2.12 (CS), U6.8 (VCC), U7.2 (D_SEL), U7.8 (~RESET), U7.9 (VCC_RF), U7.22 (V_BCKP), U7.23 (VCC), U8.2 (3V3), U9#2.13 (3.3V), U10#2.6 (VDDIO), U10#2.8 (VDD)
Board_0-+5V: C6.1, D7.1 (VDD), D8.1 (K), D9.1 (K), J3#2.A4 (VBUS), J3#2.A9 (VBUS), J3#2.B4 (VBUS), J3#2.B9 (VBUS), J14.1, LS1#2.P, M1#2.2 (+), M2#2.2 (+), M3#2.2 (+), M4.2 (+), U1#2.3 (VI)
Board_0-+BATT: C5.1, C15#2.1, D1.1 (K), J13#2.2, Q3.2 (S), Q5.2 (S), Q6#2.2 (S), R20#2.1, R24#2.1
Board_0-ADC0: J4#2.1, U3#2.7 (PA0)
Board_0-ADC1: J4#2.2, U3#2.8 (PA1)
Board_0-ADC2: J4#2.3, U3#2.9 (PA2)
Board_0-ADC3: J4#2.4, U3#2.10 (PA3)
Board_0-Buzz: R3#2.1, U3#2.3 (PC15-OSC32_OUT)
Board_0-D+: J3#2.A6 (D+), J3#2.B6 (D+), U8.14 (IO20)
Board_0-D-: J3#2.A7 (D-), J3#2.B7 (D-), U8.13 (IO19)
Board_0-EXT_INT: J2#2.3, U8.9 (IO16)
Board_0-FIRE0: Q1#2.2 (S), R16#2.2, U8.24 (IO47)
Board_0-FIRE1: Q4#2.2 (S), R23#2.2, U8.25 (IO48)
Board_0-GND: C3#2.2, C5.2, C6.2, C9.2, C10#2.2, C11.2, C12#2.2, C13#2.2, C14.2, C15#2.2, C16.2, C22#2.2, C23.2, D2.1 (K), D3#2.1 (K), D4#2.1 (K), D5.1 (K), D6#2.1 (A1), D7.3 (VSS), H1#2.1, H2.1, H3#2.1, H4#2.1, J1#2.2, J2#2.4, J2#2.MP (MountPin), J3#2.A1 (GND), J3#2.A12 (GND), J3#2.B1 (GND), J3#2.B12 (GND), J3#2.S1 (SHIELD), J4#2.5, J5.2 (Ext), J6.2, J7.2, J10.2 (Ext), J11.2, J12#2.6 (VSS), J12#2.9 (SHIELD), J14.MP (MountPin), M1#2.3 (-), M2#2.3 (-), M3#2.3 (-), M4.3 (-), Q2#2.3 (E), R5.2, R7.2, R26.2, SW1.1, TP5#2.1, U1#2.1 (GND), U2#2.2 (GND), U3#2.5 (VSS), U4#2.2 (SDX), U4#2.3 (SCX), U4#2.6 (GND), U4#2.7 (GND), U6.1 (A0), U6.2 (A1), U6.3 (A2), U6.4 (GND), U6.7 (WP), U7.10 (GND), U7.12 (GND), U7.13 (GND), U7.24 (GND), U8.1 (GND), U8.40 (GND), U8.41_1 (GND), U8.41_2 (GND), U8.41_3 (GND), U8.41_4 (GND), U8.41_5 (GND), U8.41_6 (GND), U8.41_7 (GND), U8.41_8 (GND), U8.41_9 (GND), U9#2.1 (GND), U9#2.8 (GND), U9#2.10 (GND), U10#2.1 (GND), U10#2.7 (GND)
Board_0-IMU_INT: U4#2.4 (INT1), U8.8 (IO15)
Board_0-INDI: R19.1, U8.39 (IO1)
Board_0-IO0: R2#2.2, U8.27 (IO0)
Board_0-LORA_BUSY: U8.33 (IO40), U9#2.16 (DIO2)
Board_0-LORA_D1: U8.32 (IO39), U9#2.15 (DIO1)
Board_0-LORA_RST: U8.34 (IO41), U9#2.6 (RESET)
Board_0-LORA_SS: R15.2, U8.23 (IO21), U9#2.5 (NSS)
Board_0-MISO_1: U8.30 (IO37), U9#2.2 (MISO)
Board_0-MOSI_1: U8.28 (IO35), U9#2.3 (MOSI)
Board_0-Net-(D1-A): D1.2 (A), Q6#2.1 (G), R26.1
Board_0-Net-(D2-A): D2.2 (A), R22#2.1
Board_0-Net-(D3-A): D3#2.2 (A), R19.2
Board_0-Net-(D4-A): D4#2.2 (A), R25#2.1
Board_0-Net-(D5-A): D5.2 (A), R18#2.2
Board_0-Net-(D6-A2): D6#2.2 (A2), J1#2.1, Q6#2.3 (D)
Board_0-Net-(D8-A): D8.2 (A), J11.1, U2#2.3 (VOUT)
Board_0-Net-(D9-A): D9.2 (A), J14.2, LS1#2.N, Q2#2.2 (C)
Board_0-Net-(J5-In): J5.1 (In), L2#2.2, U7.11 (RF_IN)
Board_0-Net-(J6-Pin_1): J6.1, Q3.3 (D), R22#2.2
Board_0-Net-(J7-Pin_1): J7.1, Q5.3 (D), R25#2.2
Board_0-Net-(J10-In): J9#2.1, J10.1 (In), U9#2.9 (ANT)
Board_0-Net-(J11-Pin_3): J11.3, J11.4, J13#2.3
Board_0-Net-(J13-Pin_1): J13#2.1, U2#2.1 (VIN)
Board_0-Net-(L2-Pad1): L2#2.1, R12.2
Board_0-Net-(Q1-D): Q1#2.3 (D), Q3.1 (G), R20#2.2
Board_0-Net-(Q2-B): Q2#2.1 (B), R3#2.2
Board_0-Net-(Q4-D): Q4#2.3 (D), Q5.1 (G), R24#2.2
Board_0-Net-(U6-SCL): U6.6 (SCL), U7.19 (SCL/SPI_CLK)
Board_0-Net-(U6-SDA): U6.5 (SDA), U7.18 (SDA/~SPI_CS)
Board_0-Net-(U10-CSB): R14#2.2, U10#2.2 (CSB)
Board_0-RGB: D7.4 (DIN), U3#2.17 (PA12[PA10])
Board_0-RST: R1.2, SW1.2, U8.3 (EN)
Board_0-RX1: U7.20 (TXD/SPI_MISO), U8.10 (IO17)
Board_0-SCK_1: U8.29 (IO36), U9#2.4 (SCK)
Board_0-SCL: J2#2.2, R6.2, U3#2.1 (PB7/PB8), U4#2.13 (SCL), U8.12 (IO8), U10#2.4 (SCK)
Board_0-SDA: J2#2.1, R4#2.2, U3#2.2 (PB9/PC14-OSC32_IN), U4#2.14 (SDA), U8.17 (IO9), U10#2.3 (SDI)
Board_0-SD_CLK: J12#2.5 (CLK), U8.20 (IO12)
Board_0-SD_CMD: J12#2.3 (CMD), U8.19 (IO11)
Board_0-SD_D0: J12#2.7 (DAT0), U8.21 (IO13)
Board_0-SD_D1: J12#2.8 (DAT1), U8.22 (IO14)
Board_0-SD_D2: J12#2.1 (DAT2), U8.7 (IO7)
Board_0-SD_D3: J12#2.2 (DAT3/CD), U8.18 (IO10)
Board_0-SERVO0: M1#2.1 (PWM), U3#2.11 (PA4)
Board_0-SERVO1: M2#2.1 (PWM), U3#2.12 (PA5)
Board_0-SERVO2: M3#2.1 (PWM), U3#2.13 (PA6)
Board_0-SERVO3: M4.1 (PWM), U3#2.14 (PA7)
Board_0-SWCLK: TP4#2.1, U3#2.19 (PA15/PA14-BOOT0)
Board_0-SWDIO: TP3#2.1, U3#2.18 (PA13)
Board_0-TX1: U7.21 (RXD/SPI_MOSI), U8.11 (IO18)
Board_0-cc1: J3#2.A5 (CC1), R5.1
Board_0-cc2: J3#2.B5 (CC2), R7.1
Board_1-+3V3: C3.1, C9#2.1, C10.1, C11#2.1, C12.1, C13.1, C14#2.1, C16#2.1, C22.1, C23#2.1, J2.5, J12.4 (VDD), Q1.1 (G), Q4.1 (G), R1#2.1, R2.1, R4.1, R6#2.1, R12#2.1, R14.1, R15#2.1, R16.1, R18.1, R23.1, TP1.1, TP2.1, U1.2 (VO), U3.4 (VDD), U4.5 (VDDIO), U4.8 (VDD), U4.12 (CS), U6#2.8 (VCC), U7#2.2 (D_SEL), U7#2.8 (~RESET), U7#2.9 (VCC_RF), U7#2.22 (V_BCKP), U7#2.23 (VCC), U8#2.2 (3V3), U9.13 (3.3V), U10.6 (VDDIO), U10.8 (VDD)
Board_1-+5V: C6#2.1, D7#2.1 (VDD), D8#2.1 (K), D9#2.1 (K), J3.A4 (VBUS), J3.A9 (VBUS), J3.B4 (VBUS), J3.B9 (VBUS), J14#2.1, LS1.P, M1.2 (+), M2.2 (+), M3.2 (+), M4#2.2 (+), U1.3 (VI)
Board_1-+BATT: C5#2.1, C15.1, D1#2.1 (K), J13.2, Q3#2.2 (S), Q5#2.2 (S), Q6.2 (S), R20.1, R24.1
Board_1-ADC0: J4.1, U3.7 (PA0)
Board_1-ADC1: J4.2, U3.8 (PA1)
Board_1-ADC2: J4.3, U3.9 (PA2)
Board_1-ADC3: J4.4, U3.10 (PA3)
Board_1-Buzz: R3.1, U3.3 (PC15-OSC32_OUT)
Board_1-D+: J3.A6 (D+), J3.B6 (D+), U8#2.14 (IO20)
Board_1-D-: J3.A7 (D-), J3.B7 (D-), U8#2.13 (IO19)
Board_1-EXT_INT: J2.3, U8#2.9 (IO16)
Board_1-FIRE0: Q1.2 (S), R16.2, U8#2.24 (IO47)
Board_1-FIRE1: Q4.2 (S), R23.2, U8#2.25 (IO48)
Board_1-GND: C3.2, C5#2.2, C6#2.2, C9#2.2, C10.2, C11#2.2, C12.2, C13.2, C14#2.2, C15.2, C16#2.2, C22.2, C23#2.2, D2#2.1 (K), D3.1 (K), D4.1 (K), D5#2.1 (K), D6.1 (A1), D7#2.3 (VSS), H1.1, H2#2.1, H3.1, H4.1, J1.2, J2.4, J2.MP (MountPin), J3.A1 (GND), J3.A12 (GND), J3.B1 (GND), J3.B12 (GND), J3.S1 (SHIELD), J4.5, J5#2.2 (Ext), J6#2.2, J7#2.2, J10#2.2 (Ext), J11#2.2, J12.6 (VSS), J12.9 (SHIELD), J14#2.MP (MountPin), M1.3 (-), M2.3 (-), M3.3 (-), M4#2.3 (-), Q2.3 (E), R5#2.2, R7#2.2, R26#2.2, SW1#2.1, TP5.1, U1.1 (GND), U2.2 (GND), U3.5 (VSS), U4.2 (SDX), U4.3 (SCX), U4.6 (GND), U4.7 (GND), U6#2.1 (A0), U6#2.2 (A1), U6#2.3 (A2), U6#2.4 (GND), U6#2.7 (WP), U7#2.10 (GND), U7#2.12 (GND), U7#2.13 (GND), U7#2.24 (GND), U8#2.1 (GND), U8#2.40 (GND), U8#2.41_1 (GND), U8#2.41_2 (GND), U8#2.41_3 (GND), U8#2.41_4 (GND), U8#2.41_5 (GND), U8#2.41_6 (GND), U8#2.41_7 (GND), U8#2.41_8 (GND), U8#2.41_9 (GND), U9.1 (GND), U9.8 (GND), U9.10 (GND), U10.1 (GND), U10.7 (GND)
Board_1-IMU_INT: U4.4 (INT1), U8#2.8 (IO15)
Board_1-INDI: R19#2.1, U8#2.39 (IO1)
Board_1-IO0: R2.2, U8#2.27 (IO0)
Board_1-LORA_BUSY: U8#2.33 (IO40), U9.16 (DIO2)
Board_1-LORA_D1: U8#2.32 (IO39), U9.15 (DIO1)
Board_1-LORA_RST: U8#2.34 (IO41), U9.6 (RESET)
Board_1-LORA_SS: R15#2.2, U8#2.23 (IO21), U9.5 (NSS)
Board_1-MISO_1: U8#2.30 (IO37), U9.2 (MISO)
Board_1-MOSI_1: U8#2.28 (IO35), U9.3 (MOSI)
Board_1-Net-(D1-A): D1#2.2 (A), Q6.1 (G), R26#2.1
Board_1-Net-(D2-A): D2#2.2 (A), R22.1
Board_1-Net-(D3-A): D3.2 (A), R19#2.2
Board_1-Net-(D4-A): D4.2 (A), R25.1
Board_1-Net-(D5-A): D5#2.2 (A), R18.2
Board_1-Net-(D6-A2): D6.2 (A2), J1.1, Q6.3 (D)
Board_1-Net-(D8-A): D8#2.2 (A), J11#2.1, U2.3 (VOUT)
Board_1-Net-(D9-A): D9#2.2 (A), J14#2.2, LS1.N, Q2.2 (C)
Board_1-Net-(J5-In): J5#2.1 (In), L2.2, U7#2.11 (RF_IN)
Board_1-Net-(J6-Pin_1): J6#2.1, Q3#2.3 (D), R22.2
Board_1-Net-(J7-Pin_1): J7#2.1, Q5#2.3 (D), R25.2
Board_1-Net-(J10-In): J9.1, J10#2.1 (In), U9.9 (ANT)
Board_1-Net-(J11-Pin_3): J11#2.3, J11#2.4, J13.3
Board_1-Net-(J13-Pin_1): J13.1, U2.1 (VIN)
Board_1-Net-(L2-Pad1): L2.1, R12#2.2
Board_1-Net-(Q1-D): Q1.3 (D), Q3#2.1 (G), R20.2
Board_1-Net-(Q2-B): Q2.1 (B), R3.2
Board_1-Net-(Q4-D): Q4.3 (D), Q5#2.1 (G), R24.2
Board_1-Net-(U6-SCL): U6#2.6 (SCL), U7#2.19 (SCL/SPI_CLK)
Board_1-Net-(U6-SDA): U6#2.5 (SDA), U7#2.18 (SDA/~SPI_CS)
Board_1-Net-(U10-CSB): R14.2, U10.2 (CSB)
Board_1-RGB: D7#2.4 (DIN), U3.17 (PA12[PA10])
Board_1-RST: R1#2.2, SW1#2.2, U8#2.3 (EN)
Board_1-RX1: U7#2.20 (TXD/SPI_MISO), U8#2.10 (IO17)
Board_1-SCK_1: U8#2.29 (IO36), U9.4 (SCK)
Board_1-SCL: J2.2, R6#2.2, U3.1 (PB7/PB8), U4.13 (SCL), U8#2.12 (IO8), U10.4 (SCK)
Board_1-SDA: J2.1, R4.2, U3.2 (PB9/PC14-OSC32_IN), U4.14 (SDA), U8#2.17 (IO9), U10.3 (SDI)
Board_1-SD_CLK: J12.5 (CLK), U8#2.20 (IO12)
Board_1-SD_CMD: J12.3 (CMD), U8#2.19 (IO11)
Board_1-SD_D0: J12.7 (DAT0), U8#2.21 (IO13)
Board_1-SD_D1: J12.8 (DAT1), U8#2.22 (IO14)
Board_1-SD_D2: J12.1 (DAT2), U8#2.7 (IO7)
Board_1-SD_D3: J12.2 (DAT3/CD), U8#2.18 (IO10)
Board_1-SERVO0: M1.1 (PWM), U3.11 (PA4)
Board_1-SERVO1: M2.1 (PWM), U3.12 (PA5)
Board_1-SERVO2: M3.1 (PWM), U3.13 (PA6)
Board_1-SERVO3: M4#2.1 (PWM), U3.14 (PA7)
Board_1-SWCLK: TP4.1, U3.19 (PA15/PA14-BOOT0)
Board_1-SWDIO: TP3.1, U3.18 (PA13)
Board_1-TX1: U7#2.21 (RXD/SPI_MOSI), U8#2.11 (IO18)
Board_1-cc1: J3.A5 (CC1), R5#2.1
Board_1-cc2: J3.B5 (CC2), R7#2.1

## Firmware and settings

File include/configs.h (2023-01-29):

#ifndef _CONFIG_H
#define _CONFIG_H

#include "Arduino.h"


/*--------------- BOARD_VERSIOIN_SETTING ---------------*/
// #define V1_ATMEGA328P
#define V2_ESP8266
// #define V2_ESP32
// #define V3_PIONEER

/*--------------- System function enable ---------------*/
#define USE_SERIAL_DEBUGGER
#define USE_SERIAL_COMMS
// #define GROUND_STATION
// #define GROUND_IGNITOR
#define ONBOARD_AVIONICS
#ifdef GROUND_STATION
#ifndef USE_SERIAL_DEBUGGER
#define USE_SERIAL_DEBUGGER
#endif
#ifndef USE_SERIAL_COMMS
#define USE_SERIAL_COMMS
#endif
#elif defined(ONBOARD_AVIONICS)
// #define USE_GPS_NEO6M
#define USE_PERIPHERAL_BMP280
// #define USE_PERIPHERAL_BMP280_LIB
// #define USE_PERIPHERAL_MPU6050
#define USE_GY91_MPU9250
#define USE_PERIPHERAL_BUZZER
#define PARACHUTE_TRIGGER
#define PARACHUTE_TRIGGER_2
#define DE_SPIN_CONTROL
// #define PARACHUTE_SERVO
#elif defined(GROUND_IGNITOR)
#define LAUNCH_TRIGGER
#endif

// #define USE_SERVO_CONTROL
// #define ENGINE_LOADING_TEST

#if defined(V1_ATMEGA328P) || defined(V2_ESP32)
#define USE_PERIPHERAL_SD_CARD
#define USE_LORA_COMMUNICATION
#define USE_DUAL_SYSTEM_WATCHDOG
#elif defined(V2_ESP8266) || defined(V3_PIONEER)
#define USE_WIFI_COMMUNICATION
#define USE_ESPNOW_COMMUNICATION
#define USE_FILE_SYSTEM
#endif

/*--------------------- PIN_SETTING --------------------*/
#ifdef USE_DUAL_SYSTEM_WATCHDOG
#define PIN_PARTNER_RESET 8
#endif

// Communication
// A0~A5 map to 14~19
// A0-14, A1-15, A2-16, A3-17, A4-18, A5-19
#ifdef USE_LORA_COMMUNICATION
#define PIN_LORA_INTERRUPT 3
#define PIN_LORA_BUSY A2
#define PIN_LORA_RESET A3
#define PIN_LORA_SELECT A1

#define RF_FREQUENCY 433000000  // Hz  center frequency
#define TX_OUTPUT_POWER 22      // dBm tx output power
#define LORA_BANDWIDTH \
    4  // bandwidth=125khz  0:250kHZ,1:125kHZ,2:62kHZ,3:20kHZ.... look for radio
// line 392
#define LORA_SPREADING_FACTOR 7  // spreading factor=11 [SF5..SF12]
#define LORA_CODINGRATE \
    1  // [1: 4/5,
       //  2: 4/6,
       //  3: 4/7,
       //  4: 4/8]

#define LORA_PREAMBLE_LENGTH 8            // Same for Tx and Rx
#define LORA_SYMBOL_TIMEOUT 0             // Symbols
#define LORA_FIX_LENGTH_PAYLOAD_ON false  // variable data payload
#define LORA_IQ_INVERSION_ON false
#define LORA_PAYLOADLENGTH \
    0  // 0: variable receive length
       // 1..255 payloadlength
#endif

#ifdef USE_DUAL_SYSTEM_WATCHDOG
#define PIN_SPI_CS_PARTNER 10
#endif

// PIN assignment
#ifdef V1_ATMEGA328P
#define PIN_TRIGGER_1 6
#define PIN_MOTOR 5
#ifdef USE_PERIPHERAL_BUZZER
#define PIN_BUZZER 2
#endif
#elif defined(V2_ESP8266)
#ifdef LAUNCH_TRIGGER
#define PIN_TRIGGER_1 12
#endif
#ifdef PARACHUTE_TRIGGER
#define PIN_TRIGGER_2 14
#elif defined(PARACHUTE_SERVO)
#define PIN_MOTOR 13
#endif
#ifdef PARACHUTE_TRIGGER_2
#define PIN_TRIGGER_1 12
#endif

#ifdef USE_PERIPHERAL_BUZZER
#define BUZ_ON_LEVEL 0  // Buzzer buzz on high or low
#define PIN_BUZZER 3
#endif

#define SERVO_PULSE_MIN 500
#define SERVO_PULSE_MAX 2500
#ifdef USE_SERVO_CONTROL
#define PIN_SERVO_1 0
#define PIN_SERVO_2 2
#define PIN_SERVO_3 13
#define PIN_SERVO_4 15
#endif

#elif defined(V2_ESP32)
#define PIN_TRIGGER_1 6
#define PIN_MOTOR 5
#elif defined(V3_PIONEER)
#define S0 0
#define S1 2
#define S2 15
#define PIN_CD4051 \
    13  // Every IO using CD4051 as output use "_" at the head of its name
#define _PIN_FIRE_0 5
#define _PIN_FIRE_1 7
#define PIN_MOTOR_T0 \
    14  // T0 is using ESP-07s GPIO14, therefore there is no "_" before "PIN"
#define _PIN_MOTOR_T1 \
    0  // T1 is using CD4051 IO0, therefore it use "_" at the head
#define _PIN_MOTOR_M1 1
#define _PIN_MOTOR_M2 2
#define _PIN_MOTOR_M3 3
#define _PIN_MOTOR_M4 4
#define _PIN_MOTOR_M5 6
#define PIN_INDICATOR 2
#ifdef USE_PERIPHERAL_BUZZER
#define PIN_BUZZER 0
#endif
#endif

/*------------------ WIFI Communication ------------------*/
#define AP_AS_SERVER  // Access point as server (Sky)
// #define STA_AS_SERVER  // Station as server (Ground)
#ifdef V2_ESP8266
#define WIFI_SSID "isp8266_fire"  // default ssid
#define WIFI_PASSWARD NULL        //"ESP8266_avionics"  // default passward
#define WIFI_HOST_NAME "nckuisp"  // default host name
#elif defined(V3_PIONEER)
#define WIFI_SSID "Pioneer"       // default ssid
#define WIFI_PASSWARD "Pioneer1"  // default passward
#define WIFI_HOST_NAME "nckuisp"  // default host name
#endif


/*------------ Configuration for parachute --------------*/
#define V3_1
#ifdef V3_1
#define SERVO_CLOSED_ANGLE 110
#define SERVO_RELEASE_ANGLE 170
#elif defined(V3_2)
#define SERVO_CLOSED_ANGLE 80
#define SERVO_RELEASE_ANGLE 150
#endif
#define release_by_time
#ifdef PARACHUTE_TRIGGER_2
#define CHUTE_DELAY_TIME 1000
#endif
#define RELEASE_TIME 12000
#define STOP_TIME 55000
#define PID_ON_TIME 4000
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

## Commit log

2024-04-17 feat: isp32 fix bugs
    [isp32.kicad_pcb, isp32.kicad_sch]
2024-05-03 feat: re-design schematics
    [isp32.csv, isp32.kicad_pcb, isp32.kicad_sch]
2024-07-25 chore: update isp32 project files
    [475710001.stp, CSP-USC16-TR--3DModel-STEP-468060.STEP, KSSG33J12-3.step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]
